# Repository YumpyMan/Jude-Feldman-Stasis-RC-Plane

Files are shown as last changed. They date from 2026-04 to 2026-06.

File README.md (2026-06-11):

# Jude-Feldman-RC-Plane

**Description**

My project is a completely scratch-built RC trainer plane. It has 2 main parts: the actual plane with receiver, and the controller with the transmitter. The controller has 3 inputs from the human pilot: a left stick for steering with rudder-aileron mixing, a right stick for roll and pitch control, and a slider for throttle adjustment. The transmitter uses an nRF24L01 radio module to send values to the receiver in the plane, which then tells the aileron, rudder, elevator, and ESC what to do to control the plane. All physical pieces of the plane will be printed out of LW-PLA or PLA-Aero in chunks, which will then be glued together. 

**Why I Made This Project**

I have always thought things that fly are super cool, and recently I've become super obsessed with aerospace engineering, rocketry, and model flying. However, nice RC planes are usually a few hundred bucks, and I wanted to try and make one myself. I also saw this as an opportunity to improve my maker skills, specifically CAD, programming, and electronics. Mainly, I just wanted to build something cool and this seemed like an awesome project. 

**CAD Pictures**




861F0315-AD79-403C-92D4-EF33099F7D70

**Wiring Diagrams**

Receiver
EF57DE9D-35FF-407B-82F8-F518E9ACB427

Transmitter
62B049C3-4BD3-4C83-A81A-BE357278DAD3

**BOM**
9A1BC1A5-6C3E-4660-AC9B-25DAF061A796

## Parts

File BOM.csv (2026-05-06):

Name | Purpose | Quantity | Total Cost (USD) | Link | Distributor
3mm Carbon Rods | Aileron controls | 4 | 5.29 | https://www.amazon.com/METERXITY-5-Pack-Carbon-Length-Airplane/dp/B0FBWYQMGQ | Amazon
6mm Carbon Tube | Internal structural supports | 4 | 13.50 | https://www.aliexpress.us/item/3256805393236476.html?curPageLogUid=3NeAKEdVtPZO | AliExpress
Linear Slide Potentiometer | Throttle control on transmitter | 2 | 6.79 | https://www.amazon.com/MECCANIXITY-Straight-Potentiometer-Resistors-Electronic/dp/B0DSNKK8WR?rnid=2661611011 | Amazon
ADS1115 | Allows me to connect more ADC inputs to the Picos | 1 | 7.78 | https://www.aliexpress.us/item/3256807220994755.html?curPageLogUid=7pV9VBycStcC | AliExpress
Joysticks | Pilot uses to control pitch yaw, roll, on transmitter | 5 | 6.09 | https://www.aliexpress.us/item/3256809857706441.html | AliExpress
7x4.5 Prop | Connects to motor, generates thrust | 4 | 3.25 | https://shop.addictiverc.com/products/hq-durable-prop-7x4-5-grey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 | AddictiveRC
nRF24L01 | Radio communication between transmitter and receiver | 2 | 6.56 | https://www.aliexpress.us/item/3256808584668101.html?curPageLogUid=fnnMEt52ve8q | AliExpress
Raspberry Pi Pico W | Running firmware for receiver and transmitter | 2 | 2.49 | https://www.aliexpress.us/item/3256808882158444.html?curPageLogUid=FqfpJdjte9HX | AliExpress
7.4V 2S 500mAh Lipo Battery w/JST | Powering all electrical components in the plane. | 1 | 14.94 | https://www.amazon.com/Rage-RC-500mAh-Battery-Replacement/dp/B07BH5HYDS | Amazon
MG90 9g Servos | Moving control surfaces: ailerons, rudder, elevator | 4 | 13.88 | https://www.amazon.com/Miuzei-Geared-Helicopter-Arduino-Project/dp/B0CP98TZJ2 | Amazon
30A ESC with BEC | Translates PWM input from transmitter into signals for brushless motors, supplies power output for Pico and servos. | 1 | 18.99 | https://www.amazon.com/TOYTENSI-Brushless-Motor-Plane-Airplane/dp/B0CQHLRW3D?th=1 | Amazon
MT2204-2300Kv Outrunner Motor | Produces thrust that drives the plane forwards. | 1 | 12.39 | https://www.amazon.com/Brushless-27-9x29-7mm-Electric-M5x12mm-Temperature/dp/B0F216M942?s=toys-and-games | Amazon

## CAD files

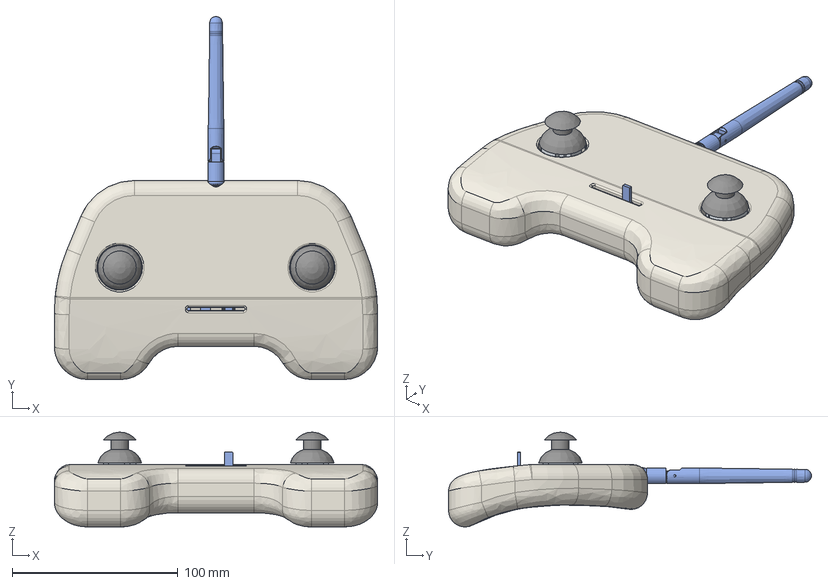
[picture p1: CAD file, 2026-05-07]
FullModels/ControllerFullAssemblyW-Components.step
195.0 x 218.8 x 57.2 mm

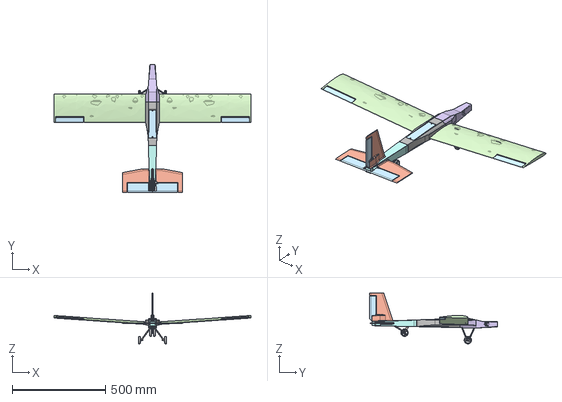
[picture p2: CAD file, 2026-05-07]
FullModels/FullAssembly.step
1056.3 x 685.8 x 272.1 mm

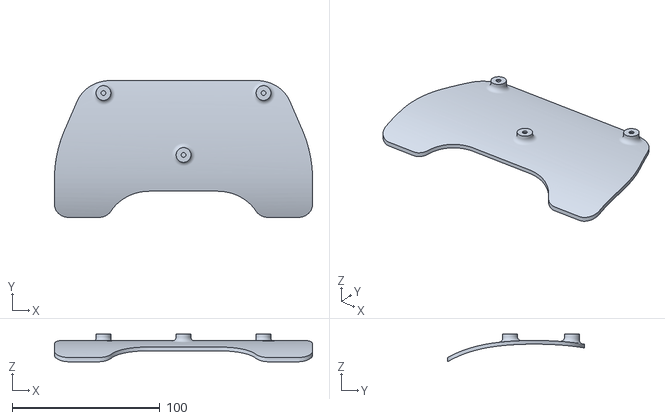
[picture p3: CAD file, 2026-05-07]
PrintableSTLFiles/Controller/ControllerPanel.stl
174.6 x 92.7 x 18.7

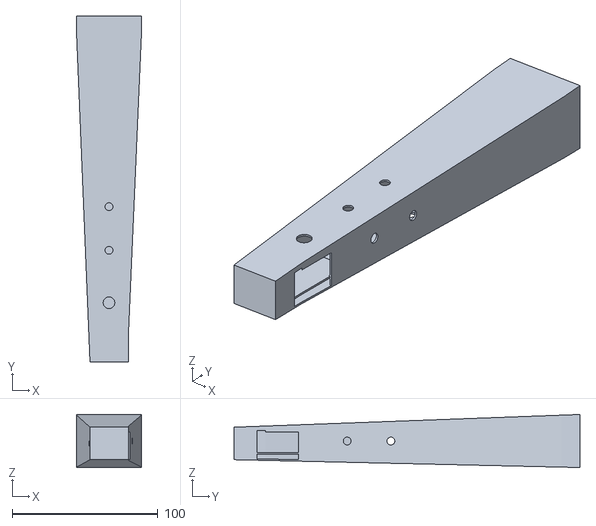
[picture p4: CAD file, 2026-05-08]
PrintableSTLFiles/FuselageAft.stl
44.5 x 237.2 x 36.4

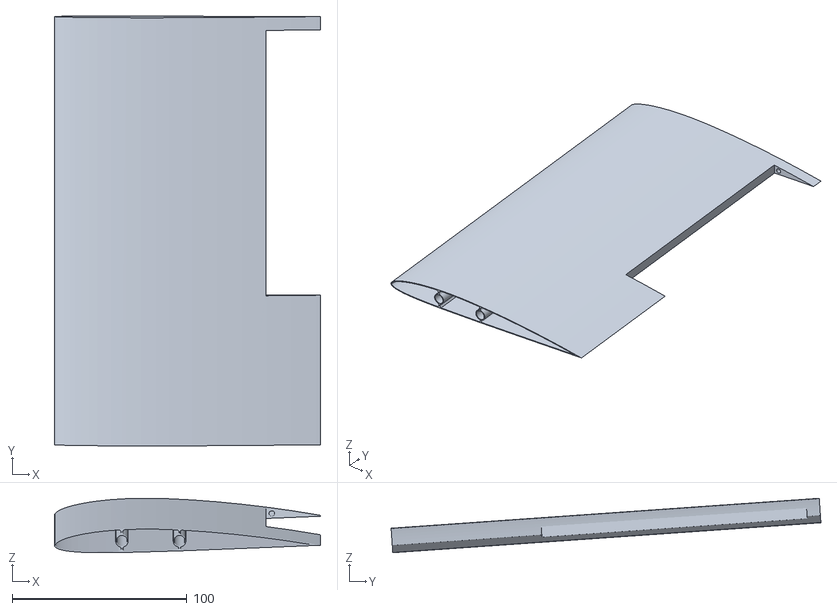
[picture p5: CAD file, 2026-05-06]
PrintableSTLFiles/Wings/Wing1R.stl
152.4 x 246.3 x 31.2

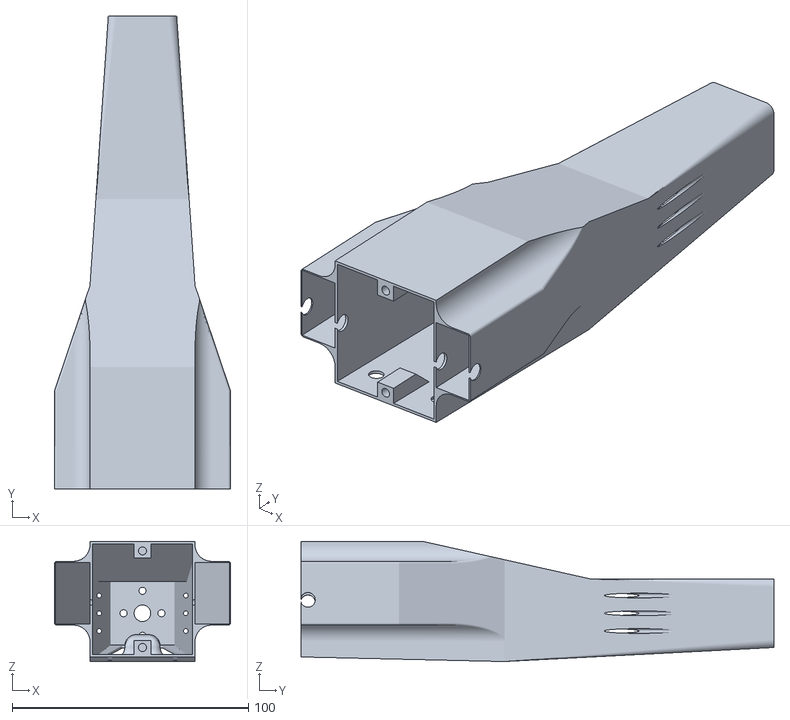
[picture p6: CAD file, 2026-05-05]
PrintableSTLFiles/FuselageFore.stl
74.5 x 200.0 x 50.8

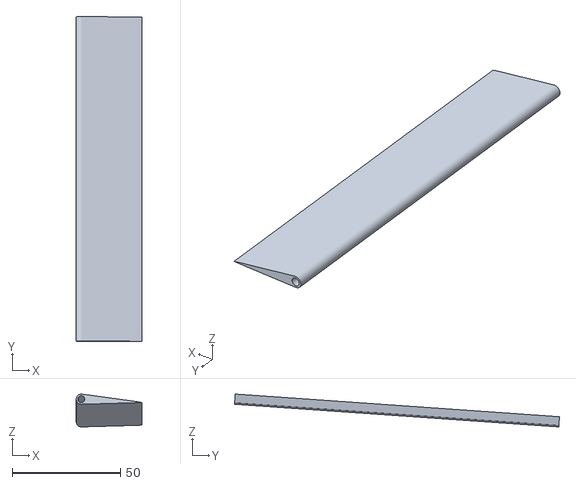
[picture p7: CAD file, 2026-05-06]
PrintableSTLFiles/Wings/AileronL.stl
30.3 x 149.8 x 15.2

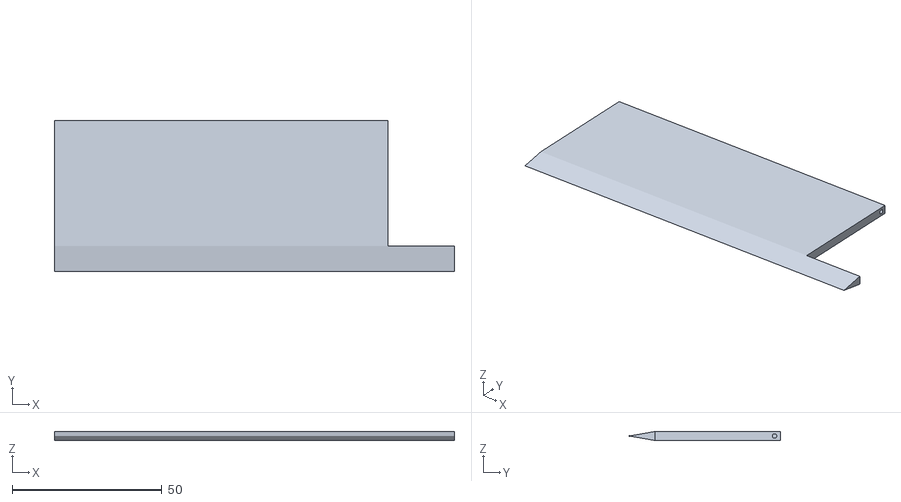
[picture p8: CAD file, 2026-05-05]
PrintableSTLFiles/ElevatorL.stl
133.4 x 50.4 x 3.00

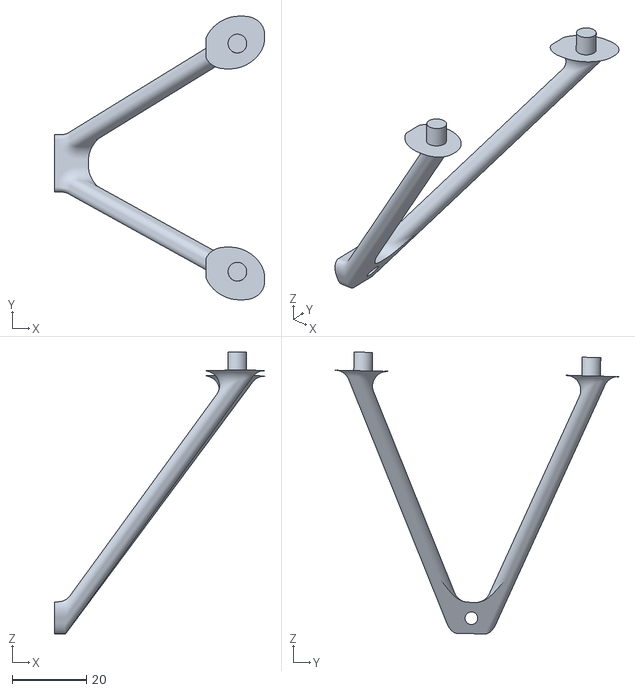
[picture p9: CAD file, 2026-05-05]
PrintableSTLFiles/ForeGearL.stl
56.5 x 76.2 x 75.8

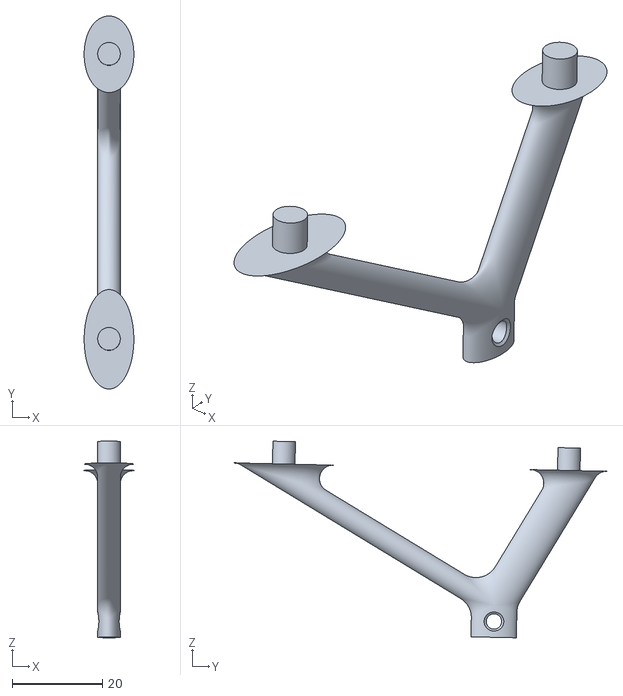
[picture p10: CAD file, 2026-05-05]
PrintableSTLFiles/GearAft.stl
11.0 x 82.5 x 43.5

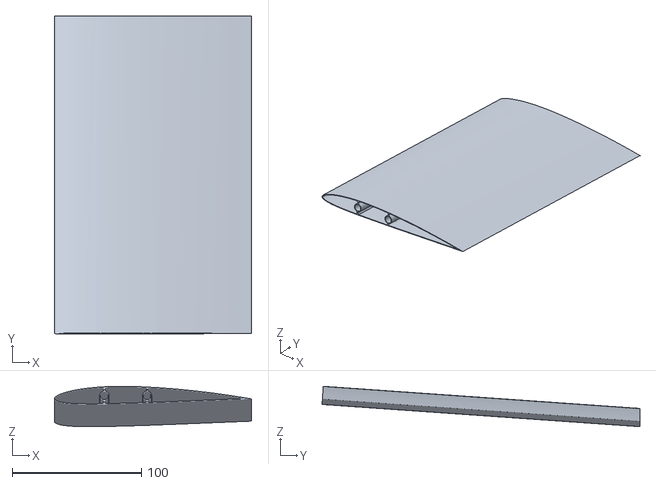
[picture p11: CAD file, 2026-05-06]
PrintableSTLFiles/Wings/Wing2L.stl
152.4 x 245.6 x 31.2

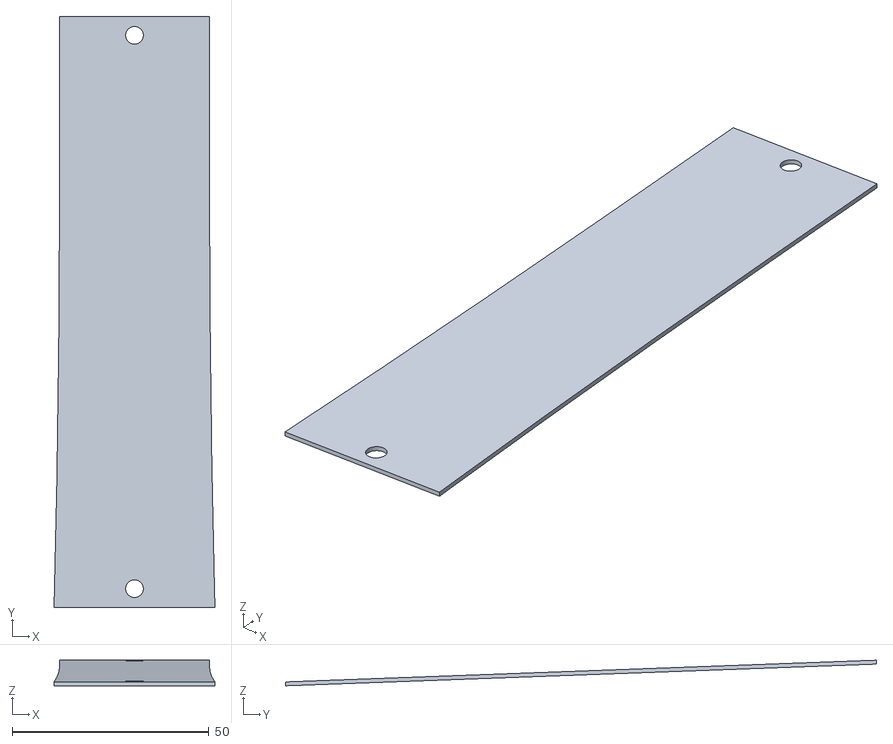
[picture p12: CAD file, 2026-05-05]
PrintableSTLFiles/TopPanel.stl
40.9 x 150.2 x 6.52

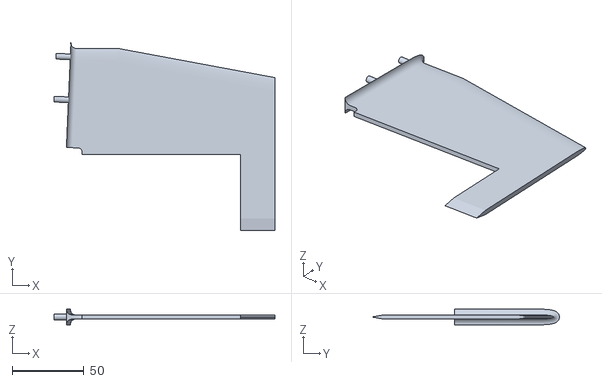
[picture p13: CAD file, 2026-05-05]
PrintableSTLFiles/HorStabR.stl
154.2 x 131.2 x 11.0

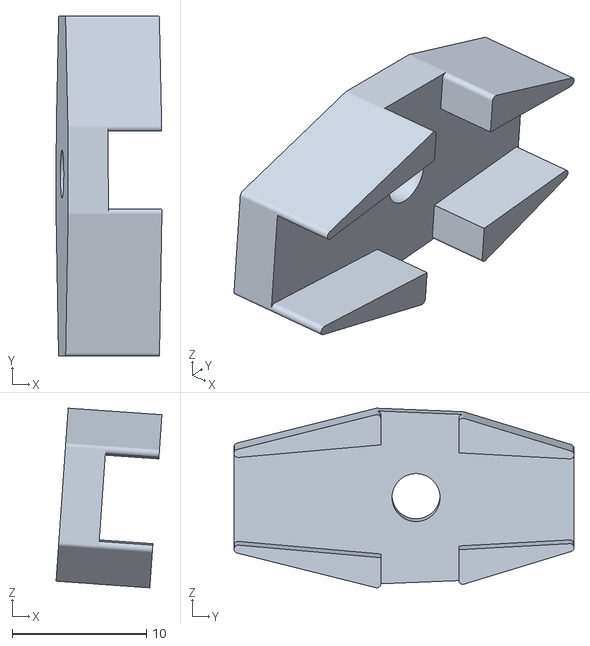
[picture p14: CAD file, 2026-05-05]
PrintableSTLFiles/ServoConnector.stl
7.88 x 25.3 x 13.4

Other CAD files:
PrintableSTLFiles/Wings/Wing1L.stl
PrintableSTLFiles/Wings/AileronR.stl
PrintableSTLFiles/Wings/Wing2R.stl
PrintableSTLFiles/ForeGearR.stl
PrintableSTLFiles/AxleAft.stl
PrintableSTLFiles/BottomPanel.stl
PrintableSTLFiles/ElevatorR.stl
PrintableSTLFiles/ForeAxleL.stl
PrintableSTLFiles/ForeAxleR.stl
PrintableSTLFiles/HorStabL.stl
PrintableSTLFiles/Rudder.stl
PrintableSTLFiles/VertStab.stl
PrintableSTLFiles/Wheel.stl

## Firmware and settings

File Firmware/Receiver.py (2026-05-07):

from machine import Pin, PWM, SPI
import utime
import struct
from nrf24l01 import NRF24L01


spi = SPI(0, baudrate=4000000, polarity=0, phase=0,
          sck=Pin(6), mosi=Pin(7), miso=Pin(4))
csn = Pin(5, mode=Pin.OUT, value=1)
ce = Pin(3, mode=Pin.OUT, value=0)
radio = NRF24L01(spi, csn, ce, payload_size=16)
radio.open_rx_pipe(1, b'\xe1\xf0\xf0\xf0\xf0')
radio.start_listening()

#turns transmitted values into pwm inputs for servos
def cleanedtopwm(value):
    return 1500 + (value * 500)

def throttletopwm(value):
    return 1000 + (value * 1000)

aileronL = PWM(Pin(2))
aileronL.freq(50)

aileronR = PWM(Pin(8))
aileronR.freq(50)

elevator_servo = PWM(Pin(9))
elevator_servo.freq(50)

rudder_servo = PWM(Pin(10))
rudder_servo.freq(50)

motor = PWM(Pin(11))
motor.freq(50)


last_packet_time = utime.ticks_ms()

while True:

    if radio.any():
        packet = radio.recv()
        aileron, elevator, rudder, throttle = struct.unpack('ffff', packet)
        last_packet_time = utime.ticks_ms()
    
    time_since_last_packet = utime.ticks_ms() - last_packet_time

    if time_since_last_packet > 250:
        aileronL.duty_ns(1500000)
        aileronR.duty_ns(1500000)
        elevator_servo.duty_ns(1500000)
        rudder_servo.duty_ns(1500000)
        motor.duty_ns(1000000)
    else: 
        aileronL.duty_ns(int(cleanedtopwm(aileron) * 1000))
        aileronR.duty_ns(int(cleanedtopwm(-aileron) * 1000))
        elevator_servo.duty_ns(int(cleanedtopwm(elevator)*1000))
        rudder_servo.duty_ns(int(cleanedtopwm(rudder) * 1000))
        motor.duty_ns(int(throttletopwm(throttle) * 1000))

    utime.sleep_ms(20)

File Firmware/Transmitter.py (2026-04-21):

from machine import ADC, Pin, SPI
import utime
import struct
from nrf24l01 import NRF24L01 


spi = SPI(0, baudrate=4000000, polarity=0, phase=0,
          sck=Pin(6), mosi=Pin(7), miso=Pin(4))
csn = Pin(5, mode=Pin.OUT, value=1)
ce = Pin(3, mode=Pin.OUT, value=0)
radio = NRF24L01(spi, csn, ce, payload_size=16)
radio.open_tx_pipe(b'\xe1\xf0\xf0\xf0\xf0')


#maps each axis to a pin on the microcontroller, ADC reads values
# throttle via ADS1115 on I2C - to be implemented with hardware
roll = ADC(Pin(26))
pitch = ADC(Pin(27))
yaw = ADC(Pin(28))
throttle_raw = 0  # placeholder until ADS1115 is wired


#converts the ADC values into values between -1 and 1
def normalize(raw):
    result = (raw / 32767.5) - 1.0  
    return result


#converts throttle ADC to values between 0 and 1
def normalize_throttle(raw):
    result = raw / 65535
    return result


#gets rid of small imperfections in readings    
def deadband(value, threshold):
    if abs(value) < threshold:
        return 0.0
    return value


#makes response less sensitive when close to the center
def expo(value, amount):
    return value**3 * amount + value * (1-amount)





#read and printed adjusted values from controller
while True:
    valueroll = roll.read_u16()
    valuepitch = pitch.read_u16()
    valueyaw = yaw.read_u16()
    
    normalizedroll = normalize(valueroll)
    normalizedpitch = normalize(valuepitch)  
    normalizedyaw = normalize(valueyaw)
    normalizedthrottle = normalize_throttle(throttle_raw)

    cleanedroll = deadband(normalizedroll, 0.05)
    cleanedpitch = deadband(normalizedpitch, 0.05)
    cleanedyaw = deadband(normalizedyaw, 0.05)
    cleanedthrottle = deadband(normalizedthrottle, 0.02)

    exporoll = expo(cleanedroll, 0.5)
    expopitch = expo(cleanedpitch, 0.5)
    expoyaw = expo(cleanedyaw, 0.5)

    #mixes some rudder input into ailerons to automatically roll while turning
    aileron_mixed = max(-1.0, min(1.0, exporoll + (expoyaw * 0.3)))

    packet = struct.pack('ffff', aileron_mixed, expopitch, expoyaw, cleanedthrottle)

    radio.send(packet)

    print(aileron_mixed, expopitch, expoyaw, cleanedthrottle)
    utime.sleep_ms(20)

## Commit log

2026-05-06 Rename RC Airplane-bom.csv to BOM.csv
    [BOM.csv]
2026-06-24 Added Assembly files
